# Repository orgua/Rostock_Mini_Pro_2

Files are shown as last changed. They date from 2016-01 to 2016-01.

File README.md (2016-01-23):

# RepRap Delta Rostock Mini Pro 2

This project offers an improved, redesigned and cleaned fork of the original sources.

### Based on the following projects:
- Rostock Mini Pro (CZAR) [thingiverse](http://www.thingiverse.com/thing:318971)
- Rostock Mini (bwevans) [thingiverse](http://www.thingiverse.com/thing:32850/) 
- Rostock (Johann) [thingiverse](http://www.thingiverse.com/thing:17175), [github](https://github.com/jcrocholl/rostock)

### Used Software: 
- [OpenSCAD](http://www.openscad.org) 2015.10.17 
- [Inkscape](https://inkscape.org) 0.91 

### Improvements in comparison to the Mini Pro:
- openSCAD-code base reworked
   - more modular design and more parametric
   - better documentation
   - cleaner code, no missing dependencies, less dead code
   - it's easier to make own mods
- included [bill of material](sources_bom/readme.md) and links (for orientation)
- included marlin-config (for orientation) 
- included redesign of [bottom and top plate](sources_inkscape/readme.md) (Inkscape svg)
- more space under the printer (there is just USB and power coming out of mine)
   - this design allows shorter wires to the motors and results in better EMC
   - shock absorbing standoffs (if printed with soft PLA)
   - better cooling for motors
   - allows active cooling for motor-drivers
- better stability, less wiggle, stiffer frame, better print-quality
   - better fin-design for all plate-connecting parts
   - design of hotend-mount is much more sturdy 
   - allow two lm8uu per rod (4 per carriage)
- the fan of the E3D-Hotend fits between hotend-mount and platform
   - hotend is lifted and print-space in z-direction is bigger 
- included space / cutout for nuts on more places
- hal-sensor-end-stops with better repeatability 
- better cable-management
- includes a filament-holder on top of the printer
- direct mounting at carriage of open belt-ends with zip-ties (with belt_mount_for_carriage.scad) 
   - groves secure belt-mount 
- built in power-switch next to the heat-bed

### Still to do: 
- include cooling into platform
- add more pictures
- further optimize the code 
- document hal-sensor-board
- motor-mount: add even more space above the motor for better cooling

### Pictures (in progress):

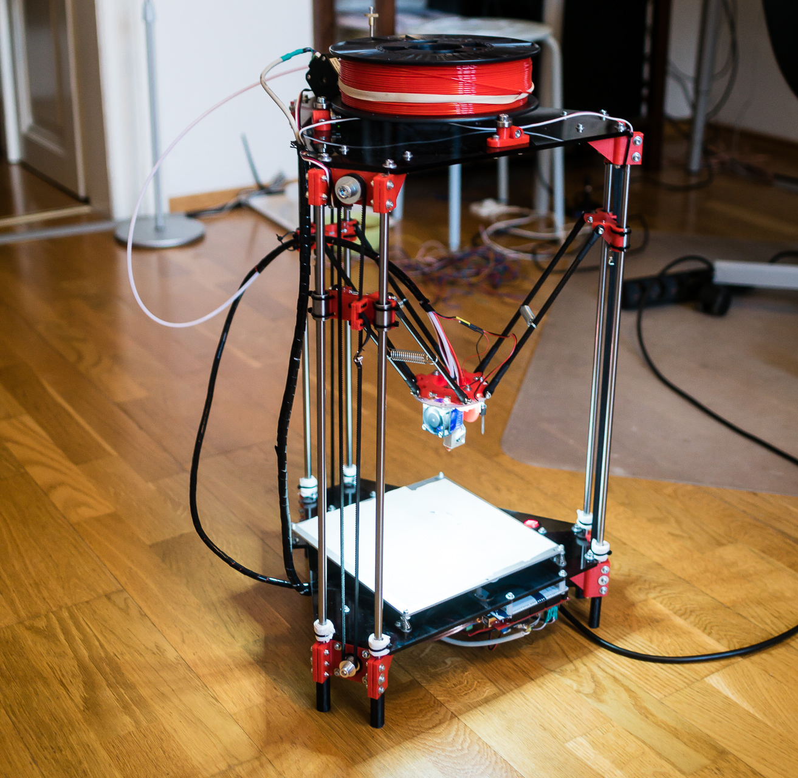
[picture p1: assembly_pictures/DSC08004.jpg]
Front


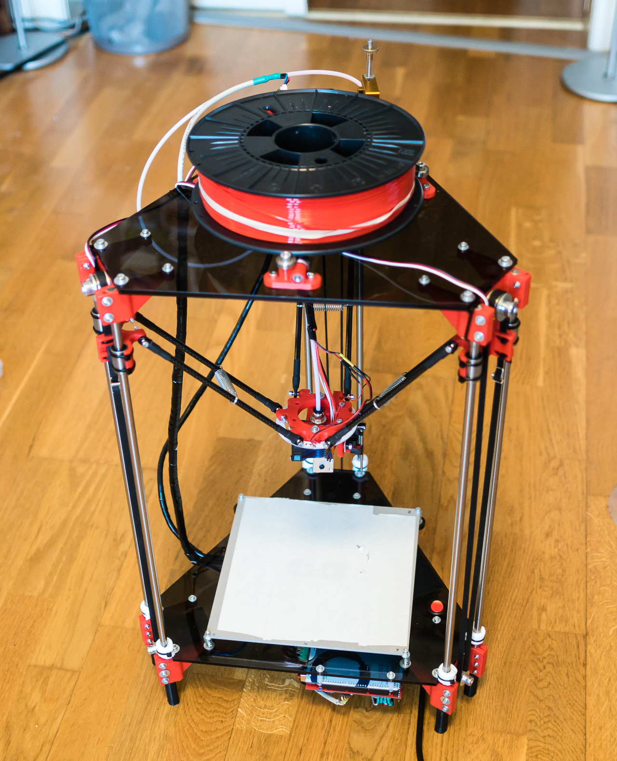
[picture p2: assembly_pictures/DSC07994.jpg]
TOP


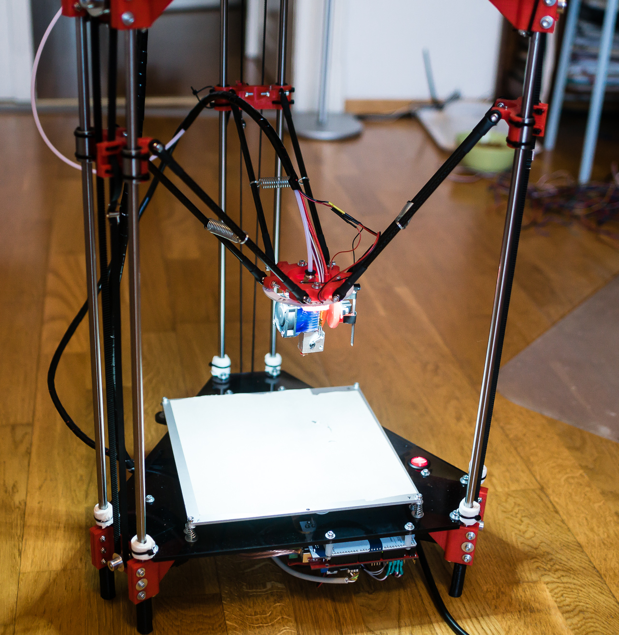
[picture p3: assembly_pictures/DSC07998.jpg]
DETAIL


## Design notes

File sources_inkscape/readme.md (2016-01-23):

# Top & Bottom Plate
- 'lasercut_all_parts' contains the design-process and also the finished parts.
- 'formulor_*' are preprocessed to meet the production-criteria for [formulor](http://www.formulor.de/)

### Design Goals:
- constructed so that you can put everything underneath the printer
- the filament and extruder sits on top of the printer (on bearings) 
- easy to change layout to fit your own parts

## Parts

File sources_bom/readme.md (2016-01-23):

# Bill of Material

### Frame / Case:
- Top & Bottom Plate 
   - 1x Acrylic Top Plate --> e.g. [Formulor Lasercut](http://www.formulor.de/)
   - 1x Acrylic Bottom Plate --> e.g. Formulor Lasercut
   - alternative: use plywood, alu, or something else what you can process 
- 16x Rostock Mini Pro Printed Parts --> print with a printer of a friend (RepRap-Style) or use shapeways

### Linear Motion
- 1x 625ZZ Bearing [Ebay](http://www.ebay.de/itm/171136285207)
- 6x linear bearing (choose one alternative):
   - LM8UU Bearing [Ebay](http://www.ebay.de/itm/370861680651)
   - Polymer bushing - Igus RJMP (expensive), RJ4JP (cheaper) [Ebay](http://www.ebay.de/itm/272087896434)
   - self lubricating copper bushing [Ali](http://de.aliexpress.com/item//32275233980.html)
- 6x 608ZZ Bearing [Ebay](http://www.ebay.de/itm/310874698319)
- 12x Traxxas 5347 U-joints	[Ebay](http://www.ebay.de/itm/231676577292)
- 3x GT-2 36 Pulley [Ebay](http://www.ebay.de/itm/181838550576)
- 3x GT-2 Timing-Belt (1m) [Ebay](http://www.ebay.de/itm/301492606404)
- 6x 8mm Hardened Zinc-coated Precision Rod (50cm) [Ebay](http://www.ebay.de/itm/161086182217)
   - alternative: standard rod 8mm (much cheaper)
- 6x 3K Carbon Fiber Tubes (>=15cm), ri=4mm
   - alternative: aluminum tube (hardware store)

### Electronics
- 3x Endstopps - choose alternative:
   - magnet hal-sensors and 3x2mm neodym magnets --> TODO: add link to osh-park
   - optical: [Ebay](http://www.ebay.de/itm/311406937622)
   - mechanical switch
- 1x RAMPS 1.4 Assembled (modified for laptop charger) 	[Ebay](http://www.ebay.de/itm/272039524081)
- Arduino Mega (came with RAMPS)
- Motordriver Drv8825 1.5A (came with RAMPS)
   - alternative: [Git](https://github.com/watterott/SilentStepStick)
- 3x Nema 17 Motor [Ebay](http://www.ebay.de/itm/231657705581)
- 1x Nema 17 Motor coupled with Planetary Gearbox 5.2:1 [Ali](http://de.aliexpress.com/item//2032350540.html)
   - alternative: nema 17 without gearbox
- 1x 12V >=200W Laptop Charger [Ebay](http://www.ebay.de/itm/151730872446)
   - alternative: withoud heatbed you need <= 100W
- heat-bed MK3 Aluminum  [Ebay](http://www.ebay.de/itm/301500250401)
- temperature sensor NTC 3950 100k (for heatbed and hotend) [Ebay](http://www.ebay.de/itm/271985790852)
- power-switch [Conrad / Datasheet](https://www.conrad.de/de/wippschalter-250-vac-10-a-2-x-ausein-sci-r13-244b-02-br-220-vac-rastend-1-st-701001.html)

### Printer-Specific Parts: 
- E3D Volcano Clone [Ali](http://de.aliexpress.com/item//32444293847.html)
- All Metal Bowden extruder	[Ali](http://de.aliexpress.com/store/product//1032650_32462527084.html)
   - alternative: print your own
- Heat-Cartridge [Ali](http://de.aliexpress.com/item//32435258474.html)
- Bowden-1.75mm	Ptfe teflon tube 2x4 mm [Ebay](http://www.ebay.de/itm/151603485581)
- Push Fitting	PC4-M6 [Ebay](http://www.ebay.de/itm/151603549528)

### Misc:
- >30x 3mm Zip-ties (hardware store)			
- Bolts, Nuts, Screws & washer: M3 M4 M5 M8	(hardware-store)
   - the following part-counts may be wrong by now		
   - M2.5: 12mm 6x
   - M3: 10mm 12x, 16mm 33x, 25mm 12x, 30mm 3x
   - M4: 12mm 6x, 16mm 18x, 30mm 2x, 50mm 6x, 70mm 6x
   - M5: 20mm 1x
   - M8: 30mm 3x

### Optional: 
- Fans:	40mm, 120mm for cooling RAMPS-Board and the printed body [Ebay](http://www.ebay.de/itm/151644447282)
- Glass-plate on the Heat-bed (Alu-Heat-bed is not plane when hot) --> use from an old picture-frame
- 3x Belt Spring Tensioner [Ebay](http://www.ebay.de/itm/191732050982)
- z-probe (select your alternative):
   - optical: see above for sensor and google for allan key z probe
   - capacitive LJ18A3-8-Z [Ebay](http://www.ebay.de/itm/351587947315)
   - if capacitive z-probe is used, then you need a 1mm steel ronde 250mm [Ebay](http://www.ebay.de/itm/262208385662)
   - electrical probing with pogopins [Ebay](http://www.ebay.de/itm/251671683856)
- 4x springs to mount the heatbed with variable distance from bottomplate (better for calibration) --> use spring from biro or look at hardwarestore
- 3x springs to hold the carbon fiber tubes together --> allows for less friction by not tightening the screws of the traxxas joints
- extra nozzles (aliexpress)
- nozzle cleaners [Ali](http://de.aliexpress.com/item//32492182891.html)
- RingLEDs	60mm inner radius [Ebay](http://www.ebay.de/itm/170508413215)
- Thermal Glue to mount heatspreader to the motordrivers [Ebay](http://www.ebay.de/itm/121564300763)
- cable wrap to tidy things up

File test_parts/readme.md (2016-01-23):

### Test Structures
- these are standard cubes 20x20x20mm, one is completely filled, the other has 1mm wall thickness
- i can recommend the following project with test-prints for calibrating your setup: http://www.thingiverse.com/thing:533472/

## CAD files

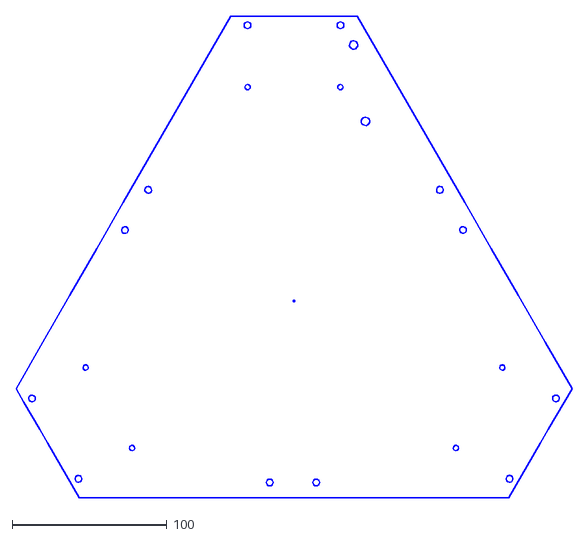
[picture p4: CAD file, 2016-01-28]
sources_inkscape/plate_top.dxf
359.3 x 311.2

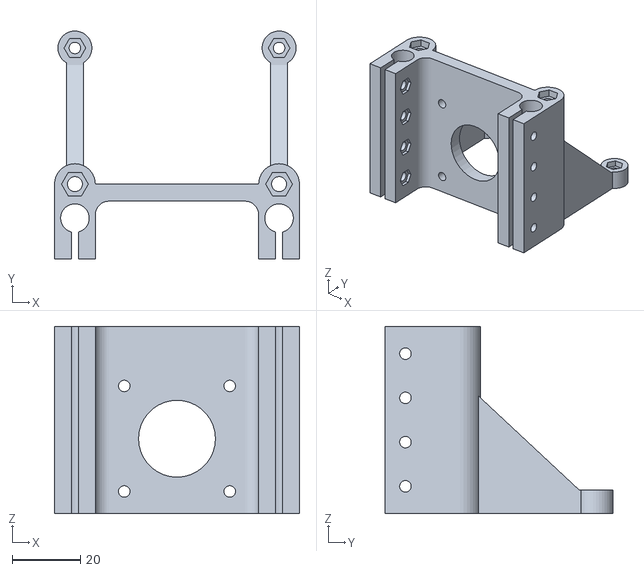
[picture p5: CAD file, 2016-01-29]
sources_openscad/motor_end.stl
72.0 x 67.0 x 55.0

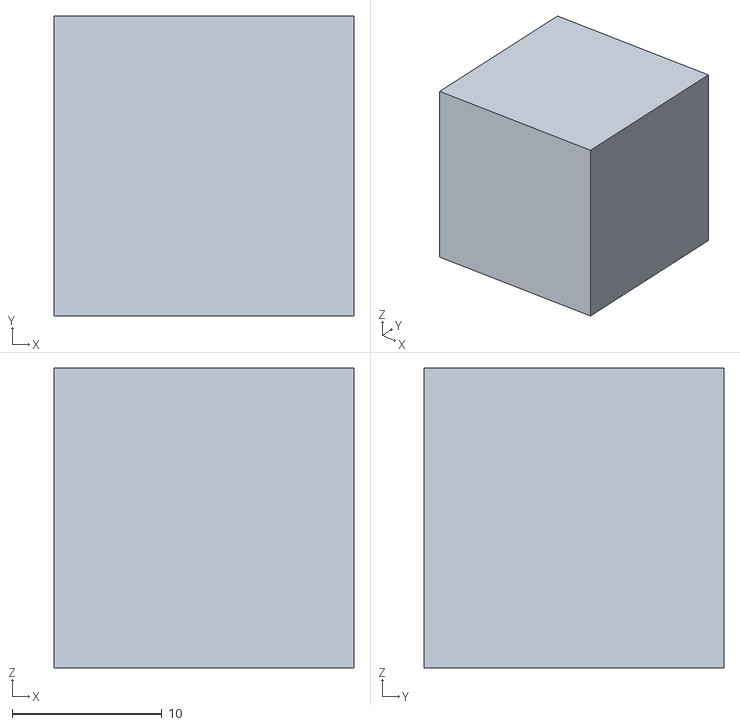
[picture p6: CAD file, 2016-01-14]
test_parts/cube-1mm.stl
20.0 x 20.0 x 20.0

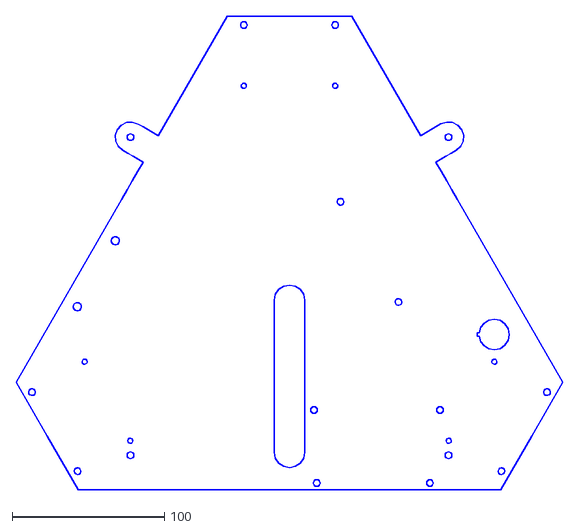
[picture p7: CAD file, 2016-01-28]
sources_inkscape/plate_bottom.dxf
359.3 x 311.2

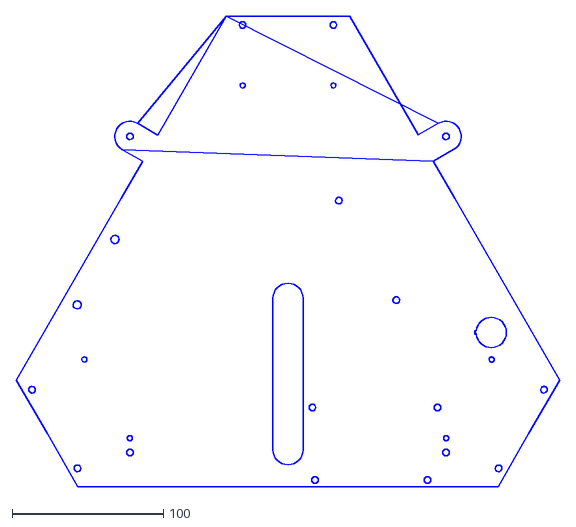
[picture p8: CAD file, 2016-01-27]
sources_openscad/plate_bottom.dxf
359.3 x 311.2

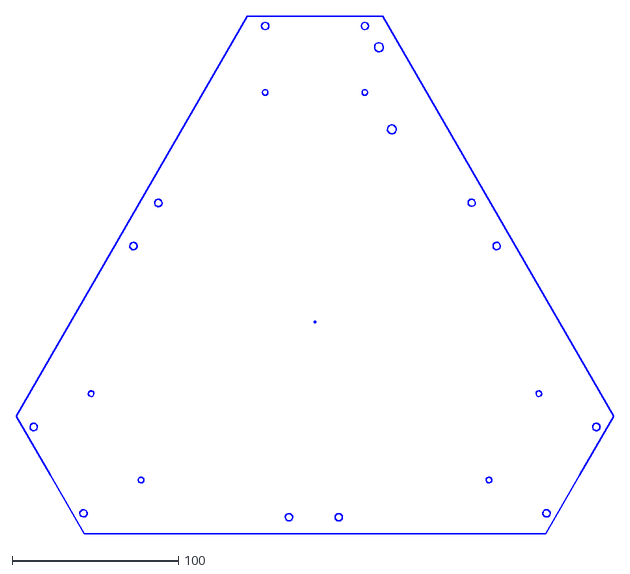
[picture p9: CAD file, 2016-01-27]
sources_openscad/plate_top.dxf
359.3 x 311.2

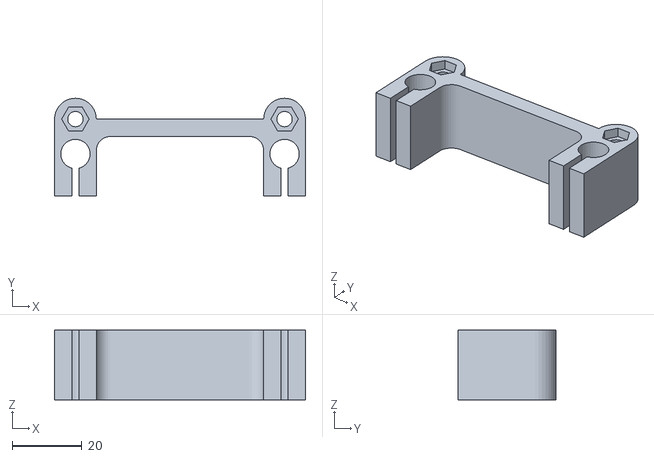
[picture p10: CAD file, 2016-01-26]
sources_openscad/bracket.stl
72.0 x 28.0 x 20.0

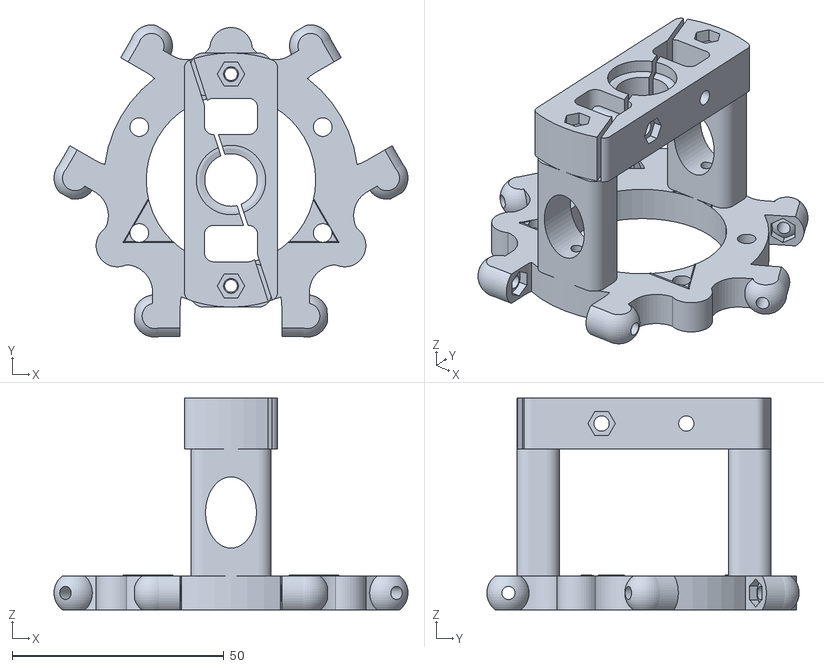
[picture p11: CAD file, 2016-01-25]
sources_openscad/debug_platform_with_hotend_mount.stl
83.6 x 73.7 x 50.0

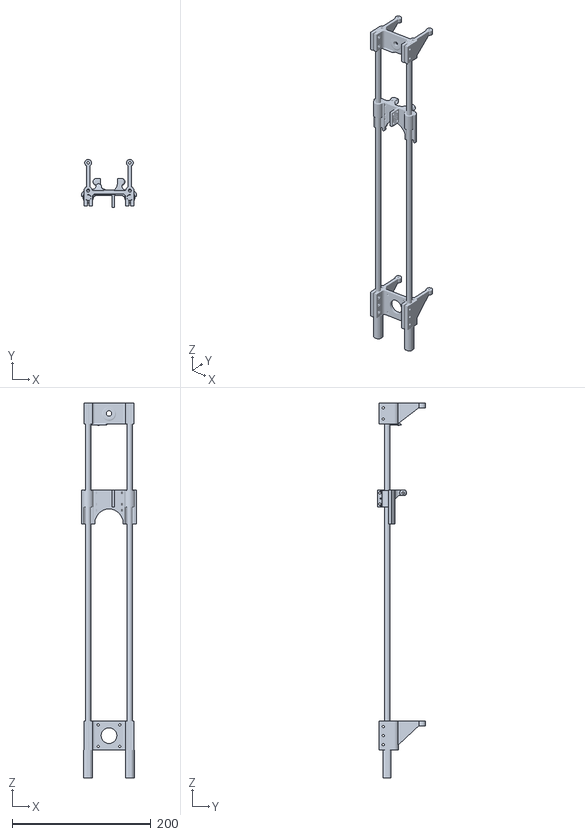
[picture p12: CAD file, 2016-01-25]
sources_openscad/debug_drive_with_carriage.stl
79.0 x 69.5 x 540.0

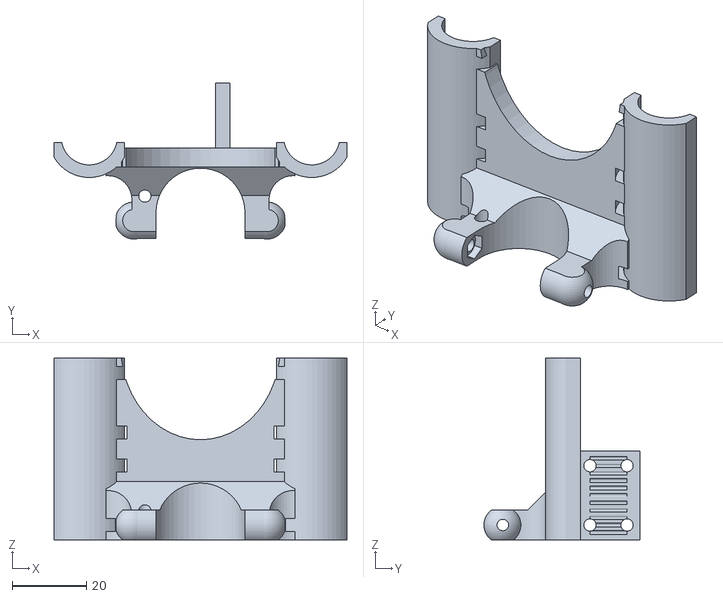
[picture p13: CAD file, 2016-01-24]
sources_openscad/carriage_for_traxxas.stl
79.0 x 42.1 x 49.0

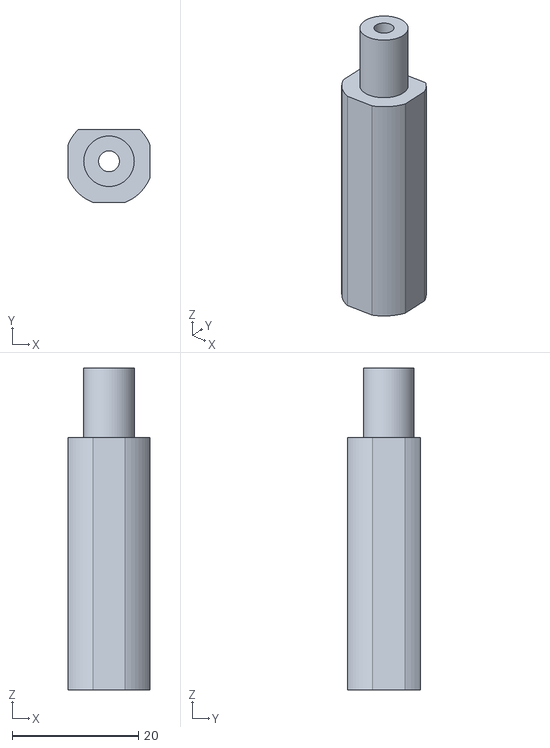
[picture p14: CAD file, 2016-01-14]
sources_openscad/motor_end_standoff.stl
13.0 x 11.5 x 51.0

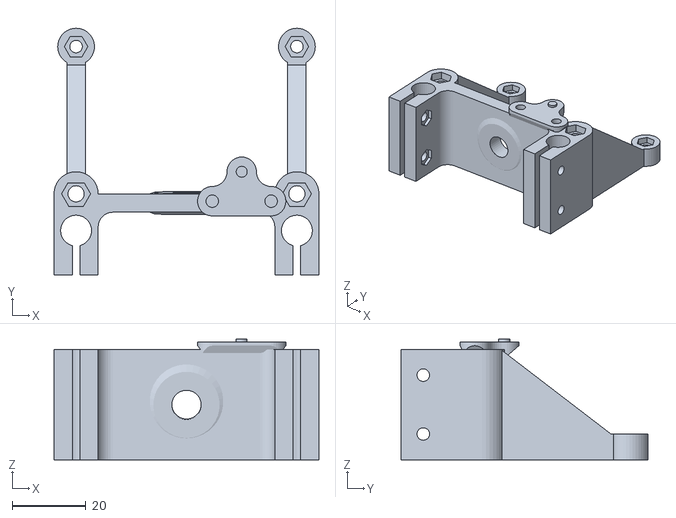
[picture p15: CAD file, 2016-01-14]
sources_openscad/idler_end.stl
72.0 x 67.0 x 32.8

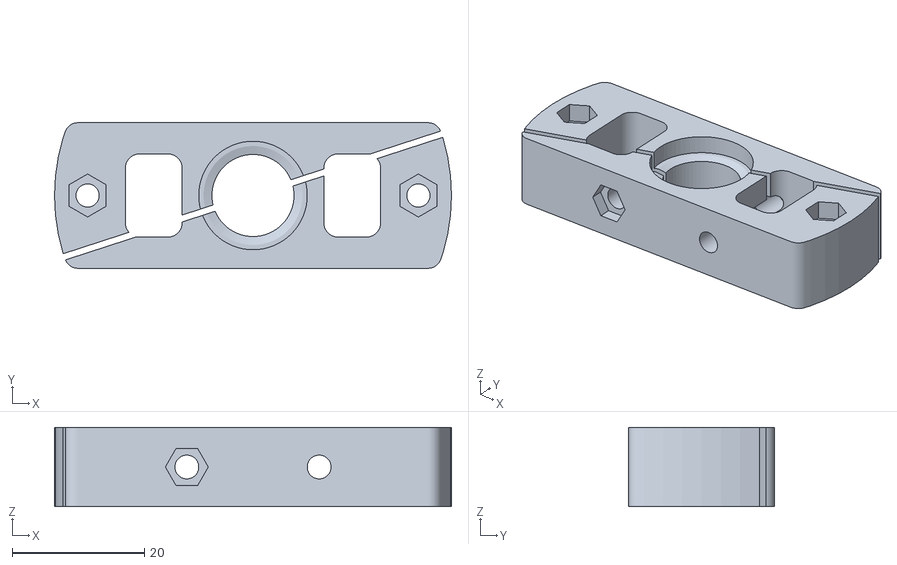
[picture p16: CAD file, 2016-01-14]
sources_openscad/hotend_mount.stl
60.0 x 22.0 x 12.0

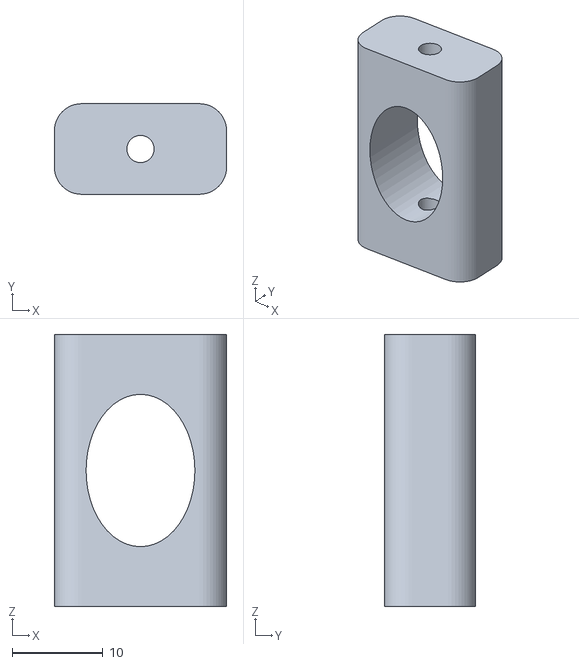
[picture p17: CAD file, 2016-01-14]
sources_openscad/hotend_mount_spacer.stl
19.0 x 10.0 x 30.0

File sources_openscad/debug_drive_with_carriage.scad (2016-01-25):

/*

This file is just for debug and shows the parts of the linear drive compiled in one view.

*/

length_rod      = 500; // mm
height_carriage = 350; //mm

use <motor_end_standoff.scad>
use <motor_end.scad>
use <carriage_for_traxxas.scad>
use <idler_end.scad>

$fn=24;

module drive_with_carriage(lr=length_rod,hc=height_carriage)
{
    r=180; // rotate affected parts one half turn
    
    // printed parts
    translate([0,0,42]) rotate([0,r,0]) motor_end();
    translate([0,0,hc]) rotate([0,r,r]) carriage();
    translate([0,0,lr]) rotate([0,r,0]) idler_end();

    for (x = [-30,+30])
    {
        // motor end standoff
        translate([x,0,0]) motor_end_standoff();
        // rod
        translate([x,0,lr/2]) cylinder(d=8, h=lr, center=true);
        // linear bearing
        translate([x,0,hc+12]) cylinder(d=15, h=24, center=true);
    }
}

drive_with_carriage();

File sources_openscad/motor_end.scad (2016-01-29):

/*
Info:
This design fits a nema17. You should print this with support, so that you get a clean motor-hole. Otherwise you could comment-out code below - look for "printable_without_support". You need 3 of these parts.

Improvement:
- better fin-design
- included space / cutout for nuts 

TODO: 
- resize part, for some air above and below the motor

*/

motor_front_dimension         = 42;
motor_front_hole_radius       = 11.3;
motor_mounting_screw_distance = 31;

printable_without_support     = false;

part_extraheight_top    =  1; // between motor and bottom-plate
part_extraheight_bottom = 12; // between motor and base

$fn=36;

include <bracket.scad>
include <misc_parts.scad>

// negative parts that get substracted
module motor_holes() 
{
    sh = 10;
    sd = motor_mounting_screw_distance/2;
    sr = M3_screw_hole_dia/2; 
    fr = motor_front_hole_radius;
    
    cylinder(r=fr, h=sh, center=true); 
    // make it printable without support!
    if (printable_without_support) 
    {
        translate([0,8,+(fr+1)/2]) rotate([0,0,45]) cube(fr, center=true);
        translate([0,8,-(fr+1)/2]) rotate([0,0,45]) cube(fr, center=true);
    }
    translate([+sd,+sd,0]) cylinder(r=sr, h=sh, center=true);
    translate([+sd,-sd,0]) cylinder(r=sr, h=sh, center=true);
    translate([-sd,+sd,0]) cylinder(r=sr, h=sh, center=true);
    translate([-sd,-sd,0]) cylinder(r=sr, h=sh, center=true);
}

//rotate([90,0,0]) motor_holes();


module motor_end() 
{
    hf  = motor_front_dimension;
    heb = part_extraheight_bottom;
    het = part_extraheight_top;
    hm  = motor_front_dimension + heb + het;
    wr  = rod_distance;

    difference() 
    {
        union() 
        {
            translate([0,0,hm/2]) bracket(hm);
            translate([+wr/2,10,0]) diagonal_fin2(35, 7, 40, 30, 5);
            translate([-wr/2,10,0]) diagonal_fin2(35, 7, 40, 30, 5);
        }
        translate([0,8,hf/2+het]) rotate([90,0,0]) motor_holes();
        for (z=[8:13:(hm-7)]) for (i=[-1,1])
            translate([i*(wr/2-6),-6, z]) rotate([0,i*90,0]) rotate([0,0,30]) screw_M3(25);
    }
}

motor_end();

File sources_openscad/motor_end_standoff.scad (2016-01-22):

/*
Info: 
You can put six of these under/in the motor_mounts in the rod-holes. I printed these with a soft PLA and put a 40mm M3-Screw inside. You need 6 of these.

Improvement: 
- wasn't there before
- shock absorbing standoffs (if printed with soft PLA)
- more space under the printer (there is just usb and power coming out of mine)
- better cooling for motors

TODO:
-
*/

h_rod   = 10;  // height 
d_rod   = 8.0; // diameter
h_stand = 40;  // standoff height
d_stand = 14;  // dia standoff

$fn=60;

module motor_end_standoff()
{
    difference() 
    {
        union() 
        {  
            translate([0,0,+h_rod/2])   cylinder(d=d_rod,  h=h_rod+2,center=true);
            translate([0,0,-h_stand/2]) cylinder(d=d_stand,h=h_stand,center=true);
        }
        
        w_cube = (d_stand - d_rod);
        
        // generate flat surfaces on each side
        translate([0,+(d_stand/2+1),  -h_stand/2]) cube([d_stand,w_cube,h_stand+2], center=true);
        translate([0,-(d_stand/2+2.5),-h_stand/2]) cube([d_stand,w_cube,h_stand+2], center=true);
        translate([+(d_stand/2+2.5),0,-h_stand/2]) cube([w_cube,d_stand,h_stand+2], center=true);
        translate([-(d_stand/2+2.5),0,-h_stand/2]) cube([w_cube,d_stand,h_stand+2], center=true);
    
        // make room to insert screws inside the standoff
        translate([0,0,-h_stand])     cylinder(d=6,h=8,center=true);
        translate([0,0,-h_stand+5.9]) cylinder(d1=6,d2=3.3,h=4,center=true);
        translate([0,0,-h_stand/2+h_rod/2]) cylinder(d=3.3,h=h_stand+h_rod+4, center=true);
    }
}

motor_end_standoff();

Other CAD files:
sources_openscad/platform.stl
sources_openscad/belt_mount_for_carriage.stl
sources_openscad/filament_holder.stl
sources_openscad/belt_mount_for_carriage.scad
sources_openscad/bracket.scad
sources_openscad/carriage_for_traxxas.scad
sources_openscad/debug_platform_with_hotend_mount.scad
sources_openscad/debug_rostock.scad
sources_openscad/filament_holder.scad
sources_openscad/hotend_mount.scad
sources_openscad/hotend_mount_spacer.scad
sources_openscad/idler_end.scad
sources_openscad/misc_parts.scad
sources_openscad/platform.scad
test_parts/cube-1mm.scad
test_parts/cube-full.scad

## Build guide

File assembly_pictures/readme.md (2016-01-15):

Pictures in progress!

Front

TOP

DETAIL

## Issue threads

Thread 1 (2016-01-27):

next steps before release

isplitt, 2016-01-27:
### For now
- [ ] build simple model of whole printer (debug_rostock)
- [ ] add more pictures
- [ ] further optimize the code
   - [ ] carriage_for_traxxas
- [ ] document hal-sensor-board
   - [ ] schematics
   - [ ] BOM
   - [ ] pictures
   - [ ] update idlers_end.scad
- [ ] motor_end: add even more space above the motor for better cooling
- [ ] update doc

### After that:
- [ ] include cooling into platform

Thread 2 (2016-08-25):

Change documentation to reflect the current condition

patuku-roy, 2016-08-25:
I think, we better change the documentation because the documentation doesn't reflect the current condition anymore, for example _"This project offers an improved, redesigned and cleaned fork of the original sources."_ .. this is not reflect the current situation, for example the `plate_top.dxf` appear in `sources_inkscape` and `sources_openscad` , this mess can really confuse when you are trying to sourcing all parts.

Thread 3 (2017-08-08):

platform and rods

tibike262, 2017-08-08:
Hello,

i am wondering if i can use the old rostock delta platform and arms with the joints for this printer as i dont want to buy the carbon rods and adapters.

Also like to ask if it is needed to modify the software for the A4988 stepper motor drivers.

Thanks,
Tibor.

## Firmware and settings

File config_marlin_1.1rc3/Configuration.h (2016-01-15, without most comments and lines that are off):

#define CONFIGURATION_H
#include "boards.h"
#include "macros.h"
#if ENABLED(USE_AUTOMATIC_VERSIONING)
  #include "_Version.h"
#else
  #include "Default_Version.h"
#endif
#define STRING_CONFIG_H_AUTHOR "orgua" // Who made the changes.
#define SHOW_BOOTSCREEN
#define STRING_SPLASH_LINE1 SHORT_BUILD_VERSION // will be shown during bootup in line 1
#define SERIAL_PORT 0
#define BAUDRATE 115200
  #define MOTHERBOARD BOARD_RAMPS_13_EFB
#define CUSTOM_MACHINE_NAME "Delta Rostock Mini Pro 2"
#define MACHINE_UUID "215e091c-32d8-4f91-ba96-754e1d7d5145"
#define EXTRUDERS 1
#define POWER_SUPPLY 1
#define TEMP_SENSOR_0 13
#define TEMP_SENSOR_1 0
#define TEMP_SENSOR_2 0
#define TEMP_SENSOR_3 0
#define TEMP_SENSOR_BED 11
#define MAX_REDUNDANT_TEMP_SENSOR_DIFF 10
#define TEMP_RESIDENCY_TIME 10  // (seconds)
#define TEMP_HYSTERESIS 3       // (degC) range of +/- temperatures considered "close" to the target one
#define TEMP_WINDOW     1       // (degC) Window around target to start the residency timer x degC early.
#define HEATER_0_MINTEMP 5
#define HEATER_1_MINTEMP 5
#define HEATER_2_MINTEMP 5
#define HEATER_3_MINTEMP 5
#define BED_MINTEMP 5
#define HEATER_0_MAXTEMP 275
#define HEATER_1_MAXTEMP 275
#define HEATER_2_MAXTEMP 275
#define HEATER_3_MAXTEMP 275
#define BED_MAXTEMP 150
#define PIDTEMP
#define BANG_MAX 255 // limits current to nozzle while in bang-bang mode; 255=full current
#define PID_MAX BANG_MAX // limits current to nozzle while PID is active (see PID_FUNCTIONAL_RANGE below); 255=full current
  #define PID_FUNCTIONAL_RANGE 10 // If the temperature difference between the target temperature and the actual temperature
  #define PID_INTEGRAL_DRIVE_MAX PID_MAX  //limit for the integral term
  #define K1 0.95 //smoothing factor within the PID
  #define  DEFAULT_Kp 20.46
  #define  DEFAULT_Ki 1.53
  #define  DEFAULT_Kd 68.38
#define MAX_BED_POWER 255 // limits duty cycle to bed; 255=full current
#define PREVENT_DANGEROUS_EXTRUDE
#define PREVENT_LENGTHY_EXTRUDE
#define EXTRUDE_MINTEMP 160
#define EXTRUDE_MAXLENGTH (X_MAX_LENGTH+Y_MAX_LENGTH) //prevent extrusion of very large distances.
#define THERMAL_PROTECTION_HOTENDS // Enable thermal protection for all extruders
#define DELTA
  #define DELTA_SEGMENTS_PER_SECOND 200
  #define DELTA_DIAGONAL_ROD 198.0 // mm
  #define DELTA_SMOOTH_ROD_OFFSET 190.0 // mm
  #define DELTA_EFFECTOR_OFFSET 33.0 // mm
  #define DELTA_CARRIAGE_OFFSET 23.0 // mm
  #define DELTA_RADIUS (DELTA_SMOOTH_ROD_OFFSET-DELTA_EFFECTOR_OFFSET-DELTA_CARRIAGE_OFFSET)
  #define DELTA_PRINTABLE_RADIUS 70
#define ENDSTOPPULLUPS // Comment this out (using // at the start of the line) to disable the endstop pullup resistors
const bool X_MIN_ENDSTOP_INVERTING = true; // set to true to invert the logic of the endstop.
const bool Y_MIN_ENDSTOP_INVERTING = true; // set to true to invert the logic of the endstop.
const bool Z_MIN_ENDSTOP_INVERTING = true; // set to true to invert the logic of the endstop.
const bool X_MAX_ENDSTOP_INVERTING = true; // set to true to invert the logic of the endstop.
const bool Y_MAX_ENDSTOP_INVERTING = true; // set to true to invert the logic of the endstop.
const bool Z_MAX_ENDSTOP_INVERTING = true; // set to true to invert the logic of the endstop.
const bool Z_MIN_PROBE_ENDSTOP_INVERTING = false; // set to true to invert the logic of the endstop.
#define DISABLE_MIN_ENDSTOPS // Deltas only use min endstops for probing.
#define X_ENABLE_ON 0
#define Y_ENABLE_ON 0
#define Z_ENABLE_ON 0
#define E_ENABLE_ON 0 // For all extruders
#define DISABLE_X false
#define DISABLE_Y false
#define DISABLE_Z false
#define DISABLE_E false // For all extruders
#define DISABLE_INACTIVE_EXTRUDER true //disable only inactive extruders and keep active extruder enabled
#define INVERT_X_DIR true // DELTA does not invert
#define INVERT_Y_DIR true
#define INVERT_Z_DIR true
#define INVERT_E0_DIR false
#define INVERT_E1_DIR false
#define INVERT_E2_DIR false
#define INVERT_E3_DIR false
#define X_HOME_DIR 1  // deltas always home to max
#define Y_HOME_DIR 1
#define Z_HOME_DIR 1
#define min_software_endstops true // If true, axis won't move to coordinates less than HOME_POS.
#define max_software_endstops true  // If true, axis won't move to coordinates greater than the defined lengths below.
#define X_MIN_POS -DELTA_PRINTABLE_RADIUS
#define Y_MIN_POS -DELTA_PRINTABLE_RADIUS
#define Z_MIN_POS 0
#define X_MAX_POS DELTA_PRINTABLE_RADIUS
#define Y_MAX_POS DELTA_PRINTABLE_RADIUS
#define Z_MAX_POS MANUAL_Z_HOME_POS
#define AUTO_BED_LEVELING_FEATURE // Delete the comment to enable (remove // at the start of the line)
  #define AUTO_BED_LEVELING_GRID  // Deltas only support grid mode.
    #define DELTA_PROBABLE_RADIUS (DELTA_PRINTABLE_RADIUS - 20)
    #define LEFT_PROBE_BED_POSITION -DELTA_PROBABLE_RADIUS
    #define RIGHT_PROBE_BED_POSITION DELTA_PROBABLE_RADIUS
    #define FRONT_PROBE_BED_POSITION -DELTA_PROBABLE_RADIUS
    #define BACK_PROBE_BED_POSITION DELTA_PROBABLE_RADIUS
    #define MIN_PROBE_EDGE 10 // The Z probe square sides can be no smaller than this.
    #define AUTO_BED_LEVELING_GRID_POINTS 5
  #define X_PROBE_OFFSET_FROM_EXTRUDER  12 // 42     // Z probe to nozzle X offset: -left  +right
  #define Y_PROBE_OFFSET_FROM_EXTRUDER  -7   // Z probe to nozzle Y offset: -front +behind
  #define Z_PROBE_OFFSET_FROM_EXTRUDER -2.35  // Z probe to nozzle Z offset: -below (always!)
  #define Z_RAISE_BEFORE_HOMING 4       // (in mm) Raise Z axis before homing (G28) for Z probe clearance.
  #define XY_TRAVEL_SPEED 4000         // X and Y axis travel speed between probes, in mm/min.
  #define Z_RAISE_BEFORE_PROBING 15   // How much the Z axis will be raised before traveling to the first probing point.
  #define Z_RAISE_BETWEEN_PROBINGS 7  // How much the Z axis will be raised when traveling from between next probing points
  #define Z_RAISE_AFTER_PROBING 50    // How much the Z axis will be raised after the last probing point.
  #define Z_SAFE_HOMING   // This feature is meant to avoid Z homing with Z probe outside the bed area.
    #define Z_SAFE_HOMING_X_POINT ((X_MIN_POS + X_MAX_POS) / 2)    // X point for Z homing when homing all axis (G28).
    #define Z_SAFE_HOMING_Y_POINT ((Y_MIN_POS + Y_MAX_POS) / 2)    // Y point for Z homing when homing all axis (G28).
  #define Z_MIN_PROBE_ENDSTOP
#define MANUAL_HOME_POSITIONS  // If defined, MANUAL_*_HOME_POS below will be used
  #define MANUAL_X_HOME_POS 0
  #define MANUAL_Y_HOME_POS 0
  #define MANUAL_Z_HOME_POS 233.80 // For delta: Distance between nozzle and print surface after homing.
#define HOMING_FEEDRATE_XYZ (40*60)
#define HOMING_FEEDRATE_E 0
#define HOMING_FEEDRATE { HOMING_FEEDRATE_XYZ, HOMING_FEEDRATE_XYZ, HOMING_FEEDRATE_XYZ, HOMING_FEEDRATE_E }
#define DEFAULT_AXIS_STEPS_PER_UNIT   {80, 80, 80, 451}  // default steps per unit for Kossel (GT2, 20 tooth)
#define DEFAULT_MAX_FEEDRATE          {500, 500, 500, 100}    // (mm/sec)
#define DEFAULT_MAX_ACCELERATION      {9000,9000,9000,10000}    // X, Y, Z, E maximum start speed for accelerated moves. E default values are good for skeinforge 40+, for older versions raise them a lot.
#define DEFAULT_ACCELERATION          3000    // X, Y, Z and E acceleration in mm/s^2 for printing moves
#define DEFAULT_RETRACT_ACCELERATION  3000    // E acceleration in mm/s^2 for retracts
#define DEFAULT_TRAVEL_ACCELERATION   3000    // X, Y, Z acceleration in mm/s^2 for travel (non printing) moves
#define DEFAULT_XYJERK                20.0    // (mm/sec)
#define DEFAULT_ZJERK                 20.0    // (mm/sec) Must be same as XY for delta
#define DEFAULT_EJERK                 5.0     // (mm/sec)
#define CUSTOM_M_CODES
    #define CUSTOM_M_CODE_SET_Z_PROBE_OFFSET 851
    #define Z_PROBE_OFFSET_RANGE_MIN -20
    #define Z_PROBE_OFFSET_RANGE_MAX 20
#define PLA_PREHEAT_HOTEND_TEMP 180
#define PLA_PREHEAT_HPB_TEMP 70
#define PLA_PREHEAT_FAN_SPEED 255   // Insert Value between 0 and 255
#define ABS_PREHEAT_HOTEND_TEMP 240
#define ABS_PREHEAT_HPB_TEMP 100
#define ABS_PREHEAT_FAN_SPEED 255   // Insert Value between 0 and 255
#define LANGUAGE_INCLUDE GENERATE_LANGUAGE_INCLUDE(en)
  #define DISPLAY_CHARSET_HD44780_JAPAN        // this is the most common hardware
#define SOFT_PWM_SCALE 0
#define FILAMENT_SENSOR_EXTRUDER_NUM 0   //The number of the extruder that has the filament sensor (0,1,2)
#define MEASUREMENT_DELAY_CM        14   //measurement delay in cm.  This is the distance from filament sensor to middle of barrel
#define DEFAULT_NOMINAL_FILAMENT_DIA 3.00  //Enter the diameter (in mm) of the filament generally used (3.0 mm or 1.75 mm) - this is then used in the slicer software.  Used for sensor reading validation
#define MEASURED_UPPER_LIMIT         3.30  //upper limit factor used for sensor reading validation in mm
#define MEASURED_LOWER_LIMIT         1.90  //lower limit factor for sensor reading validation in mm
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

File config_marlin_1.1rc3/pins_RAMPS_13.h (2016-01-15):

/**
 * Arduino Mega with RAMPS v1.3 v1.4 pin assignments
 *
 * Applies to the following boards:
 *
 *  RAMPS_13_EFB (Extruder, Fan, Bed)
 *  RAMPS_13_EEB (Extruder, Extruder, Bed)
 *  RAMPS_13_EFF (Extruder, Fan, Fan)
 *  RAMPS_13_EEF (Extruder, Extruder, Fan)
 *  RAMPS_13_SF  (Spindle, Controller Fan)
 * 
 *  RAMPS_14_EFB (Extruder, Fan, Bed)
 *  RAMPS_14_EEB (Extruder, Extruder, Bed)
 *  RAMPS_14_EFF (Extruder, Fan, Fan)
 *  RAMPS_14_EEF (Extruder, Extruder, Fan)
 *  RAMPS_14_SF  (Spindle, Controller Fan)
 *
 *  Other pins_MYBOARD.h files may override these defaults
 *
 *  Differences between
 *  RAMPS_13 | RAMPS_14
 *         7 | 11
 */

#if !defined(__AVR_ATmega1280__) && !defined(__AVR_ATmega2560__)
  #error Oops!  Make sure you have 'Arduino Mega' selected from the 'Tools -> Boards' menu.
#endif

#define LARGE_FLASH true

#ifdef IS_RAMPS_14
  #define SERVO0_PIN       11
#else
  #define SERVO0_PIN        7 // RAMPS_13 // Will conflict with BTN_EN2 on LCD_I2C_VIKI
#endif
#define SERVO1_PIN          6
#define SERVO2_PIN          5
#define SERVO3_PIN          4

#define X_STEP_PIN         54
#define X_DIR_PIN          55
#define X_ENABLE_PIN       38
#define X_MIN_PIN           3
#define X_MAX_PIN           2

#define Y_STEP_PIN         60
#define Y_DIR_PIN          61
#define Y_ENABLE_PIN       56
#define Y_MIN_PIN          14
#define Y_MAX_PIN          15

#define Z_STEP_PIN         46
#define Z_DIR_PIN          48
#define Z_ENABLE_PIN       62
#define Z_MIN_PIN          18
#define Z_MAX_PIN          19

#define E0_STEP_PIN        26
#define E0_DIR_PIN         28
#define E0_ENABLE_PIN      24

#define E1_STEP_PIN        36
#define E1_DIR_PIN         34
#define E1_ENABLE_PIN      30

#define SDPOWER            -1
#define SDSS               53
#define LED_PIN            13

#if ENABLED(FILAMENT_SENSOR)  // FMM added for Filament Extruder
  // define analog pin for the filament width sensor input
  // Use the RAMPS 1.4 Analog input 5 on the AUX2 connector
  #define FILWIDTH_PIN      5
#endif

#if ENABLED(Z_MIN_PROBE_ENDSTOP)
  // Define a pin to use as the signal pin on Arduino for the Z_PROBE endstop.
  #define Z_MIN_PROBE_PIN  18
#endif

#if ENABLED(FILAMENT_RUNOUT_SENSOR)
  // define digital pin 4 for the filament runout sensor. Use the RAMPS 1.4 digital input 4 on the servos connector
  #define FILRUNOUT_PIN     4
#endif

#if MB(RAMPS_13_EFF) || ENABLED(IS_RAMPS_EFB)
  #define FAN_PIN           9 // (Sprinter config)
  #if MB(RAMPS_13_EFF)
    #define CONTROLLERFAN_PIN  -1 // Pin used for the fan to cool controller
  #endif
#elif MB(RAMPS_13_EEF) || MB(RAMPS_13_SF)
  #define FAN_PIN           8
#else
  #define FAN_PIN           4 // IO pin. Buffer needed
#endif

#define PS_ON_PIN          12

#if ENABLED(REPRAP_DISCOUNT_SMART_CONTROLLER) || ENABLED(G3D_PANEL)
  #define KILL_PIN         41
#else
  #define KILL_PIN         -1
#endif

#if MB(RAMPS_13_EFF)
  #define HEATER_0_PIN      8
#else
  #define HEATER_0_PIN     10   // EXTRUDER 1
#endif

#if MB(RAMPS_13_SF) || ENABLED(IS_RAMPS_EFB)
  #define HEATER_1_PIN     -1
#else
  #define HEATER_1_PIN      9   // EXTRUDER 2 (FAN On Sprinter)
#endif

#define HEATER_2_PIN       -1

#define TEMP_0_PIN         13   // ANALOG NUMBERING
#define TEMP_1_PIN         15   // ANALOG NUMBERING
#define TEMP_2_PIN         -1   // ANALOG NUMBERING

#if MB(RAMPS_13_EFF) || MB(RAMPS_13_EEF) || MB(RAMPS_13_SF)
  #define HEATER_BED_PIN   -1    // NO BED
#else
  #define HEATER_BED_PIN    8    // BED
#endif

#define TEMP_BED_PIN         14   // ANALOG NUMBERING

#if ENABLED(Z_PROBE_SLED)
  #define SLED_PIN           -1
#endif
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

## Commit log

2016-01-14 add original files
    [bearing.scad, bed_clip.scad, belt.scad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]
2016-01-14 remove old rendered step-files
    [belt_clip.stl, carriage.stl, carriage_for_traxxas_ABS.stl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]
2016-01-14 reworked carriage
    [belt_mount_for_carriage.scad, carriage_for_traxxas.scad]
2016-01-14 add idler_end
    [bracket.scad, idler_end.scad]
2016-01-14 add reworked mounts for E3D-Hotends
    [hotend-mount-spacer.scad, hotend_mount.scad]
2016-01-14 add motor_end
    [motor_end.scad, motor_end_standoff.scad]
2016-01-14 added middle platform
    [platform.scad]
2016-01-14 add filament_holder
    [filament_holder.scad]
2016-01-14 added step of filament-holder
    [filament_holder.scad, filament_holder.stl]
2016-01-14 debug file that renders movable parts
    [debug_drive_with_carriage.scad]
2016-01-14 include renderings
    [belt_mount_for_carriage.stl, carriage_for_traxxas.stl, hotend-mount-spacer.stl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]
2016-01-14 add documentation
    [belt_mount_for_carriage.scad, carriage_for_traxxas.scad, hotend-mount-spacer.scad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]
2016-01-14 lasercut-parts
    cleanup needed!
2016-01-14 printable testcubes
    [cube-1mm.scad, cube-full.scad]
2016-01-14 initialize BOM
2016-01-14 improve stability and reduce print-error
    - move belt-mount to defined distance from middle (reduce error) -->
    belt_mount_offset; allow two lm8uu per rod (extra stability) -->
    carriage_extra_height
    [carriage_for_traxxas_improved.scad]
2016-01-14 improve stability and reduce print-error (this time done right)
    belt_mount_offset
    - allow two lm8uu per rod (extra stability) --> carriage_extra_height
    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
    [carriage_for_traxxas.scad, carriage_for_traxxas_improved.scad]
2016-01-14 remove unneeded files
    [bearing.scad, bed_clip.scad, belt.scad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]
2016-01-14 add preview
    [carriage_for_traxxas.stl]
2016-01-14 BOM added
2016-01-14 add test_parts
    [cube-1mm.scad, cube-1mm.stl, cube-full.scad]
2016-01-15 better documentation
    [belt_mount_for_carriage.scad, bracket.scad, carriage_for_traxxas.scad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]
2016-01-15 added unmodded config
    [Configuration.h]
2016-01-15 more config
    [Configuration_adv.h]
2016-01-15 adapt config for mini pro 2
    [Configuration.h, Configuration_adv.h]
2016-01-18 re-evaluate bom
2016-01-18 Revert "re-evaluate bom"
    This reverts commit 16ed0ff13a2b00de349992c0e95b21fbd48b760e.
2016-01-18 re evaluate BOM
2016-01-18 mention the switch
2016-01-21 fixed bug: holes for filament holder were not right
2016-01-21 rework and document
    [bracket.scad, filament_holder.scad, hotend-mount-spacer.scad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]
2016-01-21 reworked and documented
    [belt_mount_for_carriage.scad, platform.scad]
2016-01-21 rework and documentation
    [debug_drive_with_carriage.scad, motor_end_standoff.scad]
2016-01-21 rework code and add documentation
    [belt_mount_for_carriage.scad, carriage_for_traxxas.scad, hotend_mount.scad]
2016-01-22 proper code alignment
    [belt_mount_for_carriage.scad, bracket.scad, carriage_for_traxxas.scad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]
2016-01-24 carriage improvement
    [carriage_for_traxxas.scad, carriage_for_traxxas.stl]
2016-01-25 improve assembly model of linear drive
    [debug_drive_with_carriage.scad, debug_drive_with_carriage.stl]
2016-01-25 add whole platform model
    [debug_platform_with_hotend_mount.scad, debug_platform_with_hotend_mount.stl]
2016-01-26 new model of the whole printer (simple)
    [bracket.stl, debug_rostock.scad]
2016-01-27 make svg importable for openscad
    [plate_bottom.dxf, plate_top.dxf]
2016-01-28 refine model of printer
    [debug_rostock.scad, plate_bottom.dxf, plate_top.dxf]
2016-01-29 make motorend more parametrized
    [carriage_for_traxxas.scad, motor_end.scad, motor_end.stl]
